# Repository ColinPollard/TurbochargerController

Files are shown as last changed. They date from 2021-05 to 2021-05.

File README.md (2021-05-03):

# TurbochargerController: Colin Pollard, McKay Mower, Luke Majors
An absolute pressure turbocharger controller, suited for aircraft use. 

---
## Overview:
All turbocharger systems have a wastegate valve which actuates based on the pressure generated by the turbine. If this pressure exceeds a limit, the wastegate opens to let some of this air out of the system, preventing potential damage to the engine. In cars and other ground-based vehicles, this valve can be mechanical where an actuator measures the difference between outside air and the pressurized air from the turbo. If this differential gets to be too large, the valve opens. A problem arises when using this type of system on an airborne unit since the air density is not fixed. If the outside pressure drops due to alitutde, the wastegate valve can be open for longer than intended since the pressure differential will be always be high. 

The solution is to use an absolute pressure reading. While this can be acomplished by utilizing a mechanical unit, there are advantages to being able to set the desired output pressure from the turbocharger, such as setting efficient cruise power levels and optimizing the range of operation of the turbocharger based on altitude. For this, an electronic solution is needed.

For this implementation, there are two major devices. The first is a raspberrypi based display that handles all inputs from the user. This device will send desired valve positions and receive pressure and status back over RS232. The second device is an STM32 based unit that collects and processes sensor data, while driving the valves to the desired positions as commanded by the raspberrypi. An absolute pressure sensor is used to measure the downstream pressure from the turbocharger. A stepper motor is used to drive the slow-moving wastegate valve, while a PWM signal is used to pulse the fast-moving bypass solenoid valve. All connections are routed through a DE9 connector using a custom wiring harness.

## Demonstration:
https://www.youtube.com/watch?v=gG7AOT28C98

## Software Design:
* RS232 Communication is handled through timers and interrupts. On receiving a command to move valve positions, an interrupt is triggered that sets desired position variables that are handled elsewhere. The systick interrupt is modified to send a status packet back to the pi every 2 seconds. 
* Stepper motor movement is handled on a timer, where position is tracked using an open loop controller. Every 10 miliseconds, the motor will move if there is an error between the current position and the desired position. The timer interval can be changed to increase or decrease the rate at which the motor moves. 
* The solenoid bypass valve is driven directly using the general timer 2 peripheral. A 30Hz carrier frequency is driven using a prescaled system clock. The duty cycle of this signal is updated on receiving a command from the pi.
* The pressure sensor is read from the ADC in a continuous conversion mode. The value is read during the RS232 transmission timer update.

## Hardware Design:
### Microcontroller
The microcontroller selected for this project is the NucleoL412KB. This is an STM32 board based around the cortex M4 core, packaged inside an arduino nano form factor. This was preferable for our project, since two headers can be placed on the PCB instead of a full microcontroller implementation. Pins were selected such that the timer peripheral, analog to digital converter, USART, and GPIO could be utilized most effectively for each of the applications below. Power to the system is supplied through the external 5v input, 3.3V power is generated through the MCU's onboard voltage regulator.

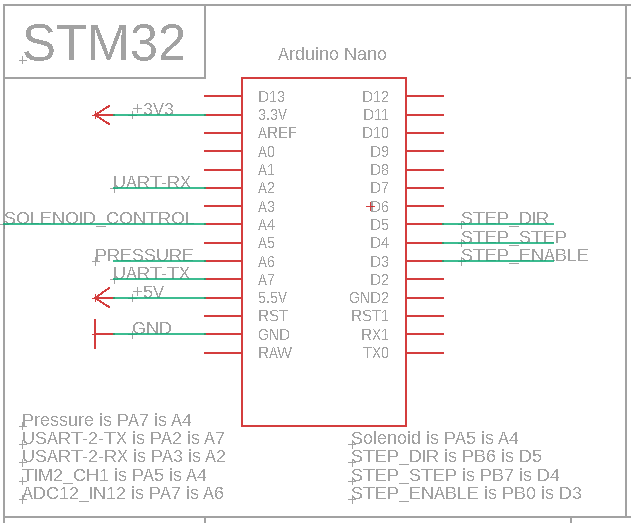
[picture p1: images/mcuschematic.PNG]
MCU Schematic


### Pressure Sensor
The pressure sensor used in this design is the NPP301. This sensor is an absolute pressure sensor capable of sensing up to 100psi. The device acts as a wheatstone bridge, where the resistance varies based on pressure. The sensor is connected to a two-stage amplifier stage, with a potentiometer available for sensitivity adjustment. This output feeds into the ADC12_channel1 of the microcontroller. 

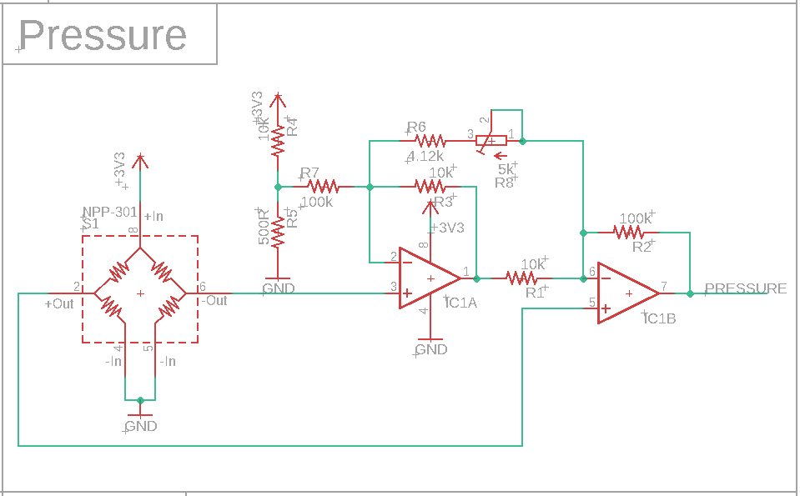
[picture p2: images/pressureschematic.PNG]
Pressure Sensor Schematic


### Stepper Motor Driver:
The stepper motor driving stage is created using an A4988 "Stepstick" shield. Three general purpose output pins are used to drive the enable, direction, and step pins. The output of the motor is routed to a four-place screw terminal block for easy wiring to motors. Microstepping settings are selectable using a semi-permanent solder bridge feature on the back of the board. Power for the stepper motor is supplied through a separate motor supply line through the DE9.

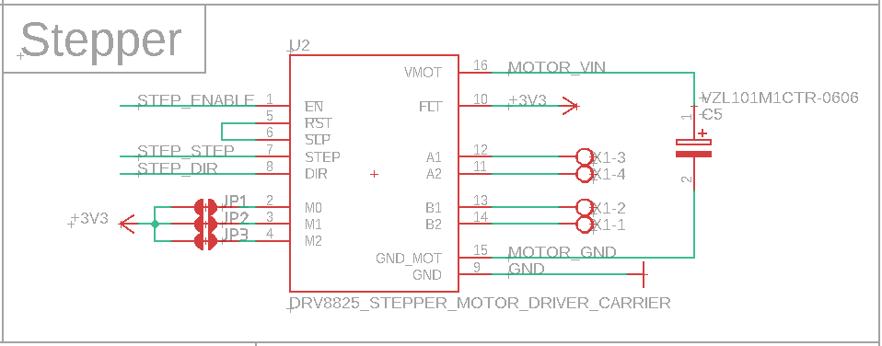
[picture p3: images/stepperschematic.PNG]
Stepper Motor Schematic


### Solenoid Driver
The bypass valve is actuated using a 12v 32Hz PWM signal. In order to drive this load, a BJT driving stage was designed for this specific load and microcontroller. A diode is included on the load circuit to prevent reverse current due to the inductance of the solenoid valve. The base of the BJT is driven through a resistor by the general purpose TIM2_CH1. Power for driving the solenoid is sourced from an external high current supply pin through the DE9.

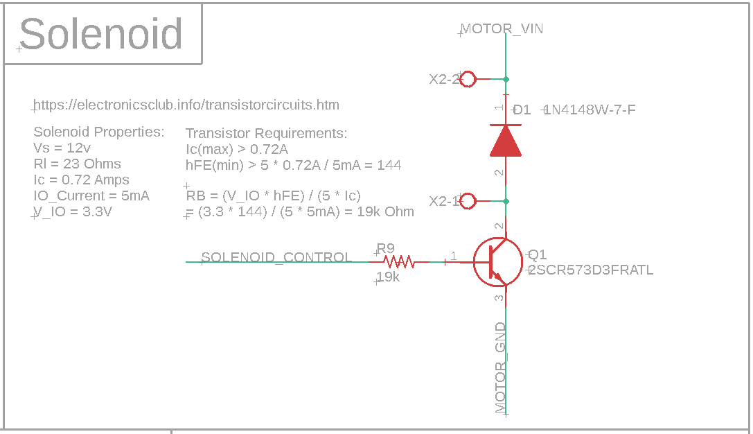
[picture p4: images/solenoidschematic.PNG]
Solenoid Driver Schematic


### RS232 Communications
A MAX3232 RS232 driver was utilized to convert the UART signal from the microcontroller to RS232 levels. This converter utilizes four external 0.1uF capacitors with a charge pump to increase the 3.3V supply to the correct level for communication.

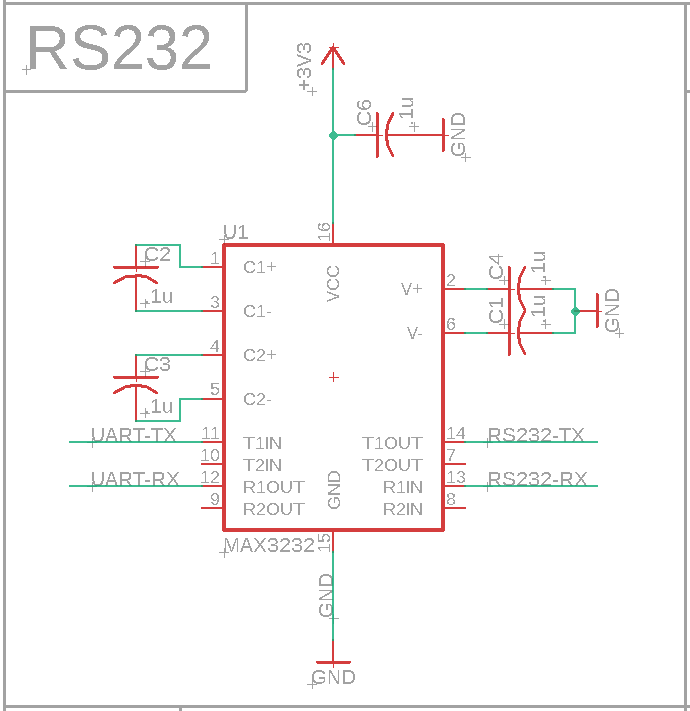
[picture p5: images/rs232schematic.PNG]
RS232 Driver Schematic


---

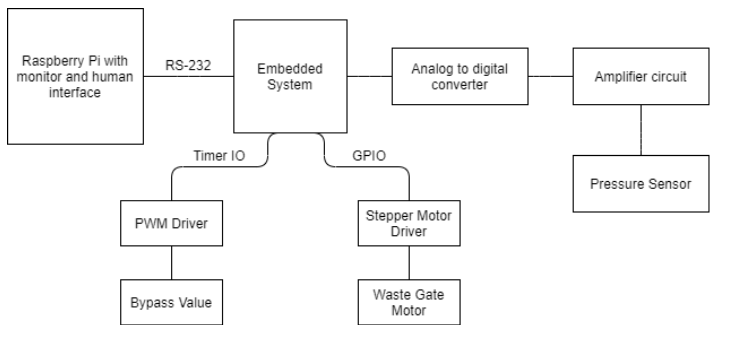
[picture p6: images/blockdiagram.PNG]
Block Diagram


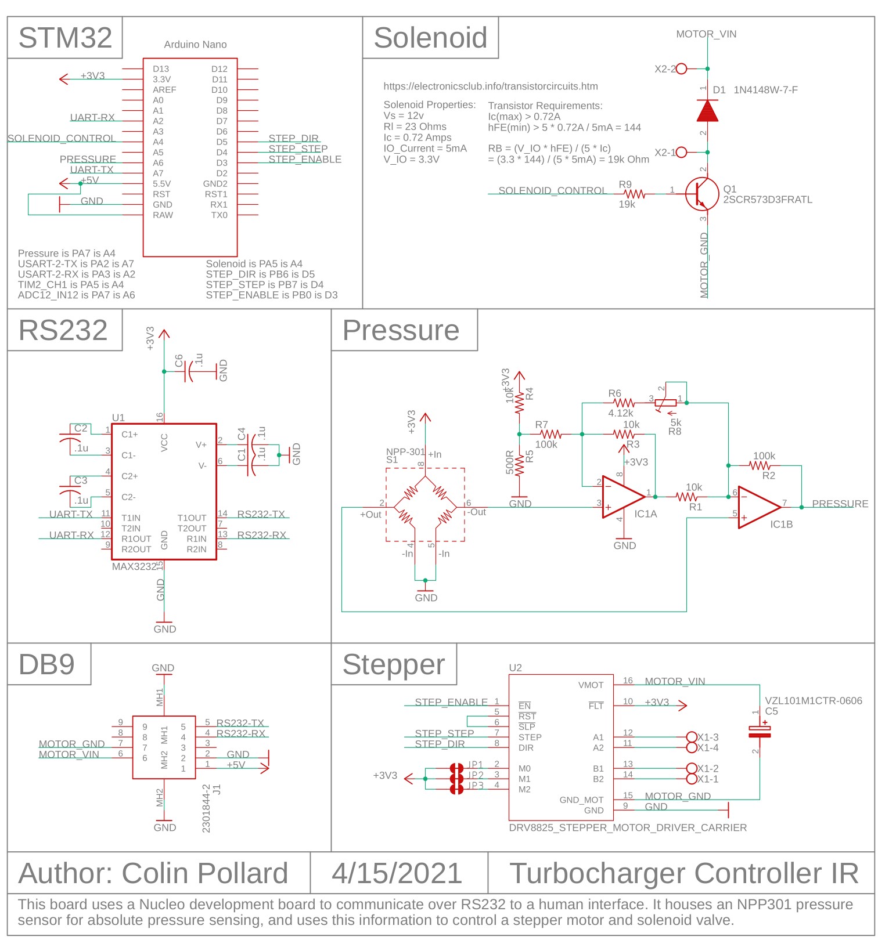
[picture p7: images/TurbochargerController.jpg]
Schematic


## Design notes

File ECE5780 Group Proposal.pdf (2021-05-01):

Turbocharger Controller Project Proposal

ECE 5780

3/18/2021

Members: Colin Pollard, McKay Mower, Luke Majors

Project Background:

One common problem in aviation is that combustion engines lose power at high altitudes

due to the decreased air density. Turbochargers provide a solution to this by harvesting energy

from the engine’s exhaust to compress the intake air. This increases the density, and allows for

more fuel to be burnt at high altitudes.

One challenge with this type of system is that the turbocharger can pressurize the air too

much, causing the engine to experience extreme stresses. This is mitigated using a waste-gate

valve. Essentially, pressurized air is allowed to escape to the atmosphere, instead of into the

engine intake. In cars, a mechanical piston can be utilized to control the position of this valve.

The piston measures the relative pressure between the outside air, and the compressed intake air.

When the intake air is a certain pressure above the outside air, the piston opens the valve. This

technique does not work in an aircraft, however. Since the outside pressure can be very low due

to high altitudes, the valve would be stuck in an open position the majority of the time. A

different solution is needed.

Abstract:

The goal of this project is to design an embedded system that measures the absolute

pressure created by the turbocharger, and actuate two valves to maintain the pressure below a

value set by the pilot.

Technical Specification:

- The pressure setting will be sent via an RS232 from an external human interface device

(Raspberry Pi with display and mouse). It will be converted to a 3.3 Volt UART

connection through the use of a MAX3232.

- The first valve, the bypass valve, is a 12V solenoid that is pulse width modulated at

32Hz. This will be controlled by an onboard timer that drives an external MOSFET to

switch the higher voltage signal.

- The second valve, the waste-gate valve, is manipulated through a NEMA 17 Stepper

motor. This will be driven by two GPIO pins, and an A4988 motor driver.

- The pressure sensor is an analog whetstone device, whose reading will be amplified

through a differential op-amp circuit, and then fed into an onboard ADC.

- A NUCLEO-L412KB will be utilized as the microcontroller.
- A custom circuit board will be created to house the amplification and driving circuitry,

with connectors to interface with the valves, pressure sensor, and RS232 link.

Hardware Block Diagram:

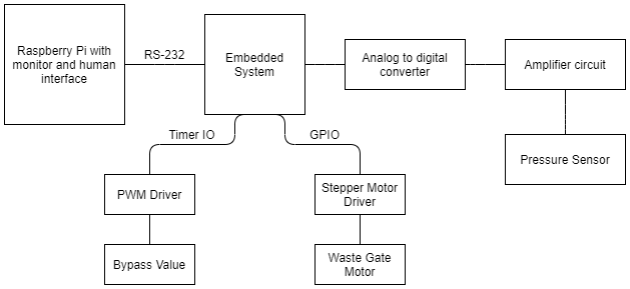
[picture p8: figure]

Software Block Diagram:

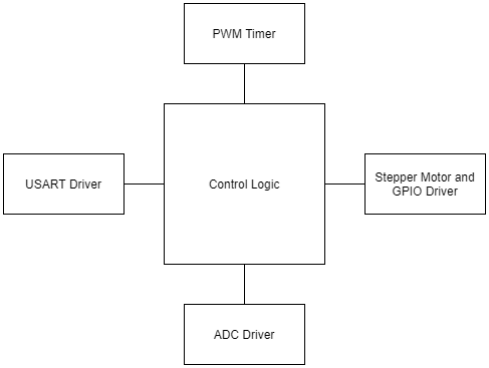
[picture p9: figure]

Milestone achievements:

1. RS232 and Stepper Motor Driver Integration
- Send and receive dummy data (pressure readings, desired pressure, valve

positions) between the embedded system and the raspberry pi.

- Configure general purpose input output pins to drive a stepper motor using the

A4988.

2. PWM Integration
- Configure a timer to produce a 32Hz PWM signal.
- Step the logic level signal up to a 12V power signal using a MOSFET driver.
3. Pressure Sensor Integration
- Design an amplification stage for the pressure sensor to scale to 0-3.3V

- Configure an analog input to accept the signal.
- Calibrate the pressure sensor to known pressure values.
4. Final integration testing and demo
- Integrate the RS232 link to actuate the valves, send pressure readings (transition

from dummy data).

- Verify overall functionality.

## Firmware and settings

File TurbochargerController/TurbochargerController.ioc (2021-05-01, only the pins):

Mcu.UserName=STM32L412KBUx
PA0-CK_IN.Signal=RCC_CK_IN
PA2.GPIO_Label=USART2_TX
PA2.Signal=USART2_TX
PA3.GPIO_Label=USART2_RX
PA3.Signal=USART2_RX
PA5.GPIO_Label=Solenoid_Control
PA5.Signal=GPIO_Output
PA7.Signal=ADCx_IN12
PB0.GPIO_Label=Step_Enable
PB0.Signal=GPIO_Output
PB6.GPIO_Label=Step_Dir
PB6.Signal=GPIO_Output
PB7.GPIO_Label=Step_Step
PB7.Signal=GPIO_Output

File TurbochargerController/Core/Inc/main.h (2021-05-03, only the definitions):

#define USART2_TX_Pin GPIO_PIN_2
#define USART2_TX_GPIO_Port GPIOA
#define USART2_RX_Pin GPIO_PIN_3
#define USART2_RX_GPIO_Port GPIOA
#define Solenoid_Control_Pin GPIO_PIN_5
#define Solenoid_Control_GPIO_Port GPIOA
#define Step_Enable_Pin GPIO_PIN_0
#define Step_Enable_GPIO_Port GPIOB
#define SWDIO_Pin GPIO_PIN_13
#define SWDIO_GPIO_Port GPIOA
#define SWCLK_Pin GPIO_PIN_14
#define SWCLK_GPIO_Port GPIOA
#define LED_Pin GPIO_PIN_3
#define LED_GPIO_Port GPIOB
#define Step_Dir_Pin GPIO_PIN_6
#define Step_Dir_GPIO_Port GPIOB
#define Step_Step_Pin GPIO_PIN_7
#define Step_Step_GPIO_Port GPIOB

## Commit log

2021-05-01 Added eagle PCB files.
    [TurbochargerController IR.brd, TurbochargerController IR.sch]
2021-05-01 Added support for sending ADC values
2021-05-02 UART parsing work.
2021-05-02 Verified uart parsing.
2021-05-03 Motor moving from uart.
2021-05-03 Updated ADC Init
2021-05-03 Implemented PWM
2021-05-03 Changed ADC init
2021-05-03 Motor moving from.

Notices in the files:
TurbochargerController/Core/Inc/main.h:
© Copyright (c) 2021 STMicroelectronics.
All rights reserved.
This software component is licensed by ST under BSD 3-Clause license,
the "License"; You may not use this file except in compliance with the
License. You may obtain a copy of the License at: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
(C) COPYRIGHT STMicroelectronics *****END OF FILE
